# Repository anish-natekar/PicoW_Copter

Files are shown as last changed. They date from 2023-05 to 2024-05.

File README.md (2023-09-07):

# PicoW_Copter

My Pico W Copter (ignore the rubber band)

Affordable micro sub 100g coreless motor quadcopter made using Raspberry Pi pico W and controlled via an APP through WiFi.

OSHW lab - https://oshwlab.com/anishsan/picocopter
(the connectors might be different Please check the connectors for the battery separately)

First test flight (IT WORKS!!!) - https://www.youtube.com/shorts/tu2c7LCsRs8

Documentation link (Still working on this) - https://picow-copter-docs.readthedocs.io/en/latest/

APP to control PicoW Copter - [UDP Joystick](https://udpjoystick.en.aptoide.com/app) 
. delete Aptoid APP after installtion and just keep UDP Joystick APP 

Settings for the Android APP UDP joystick

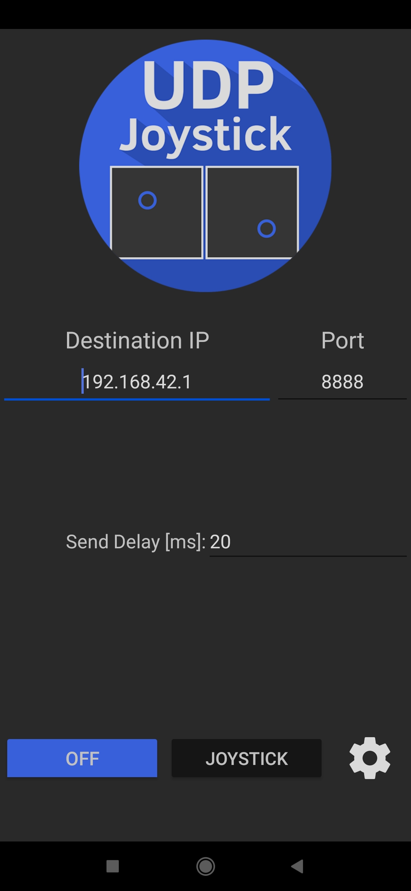
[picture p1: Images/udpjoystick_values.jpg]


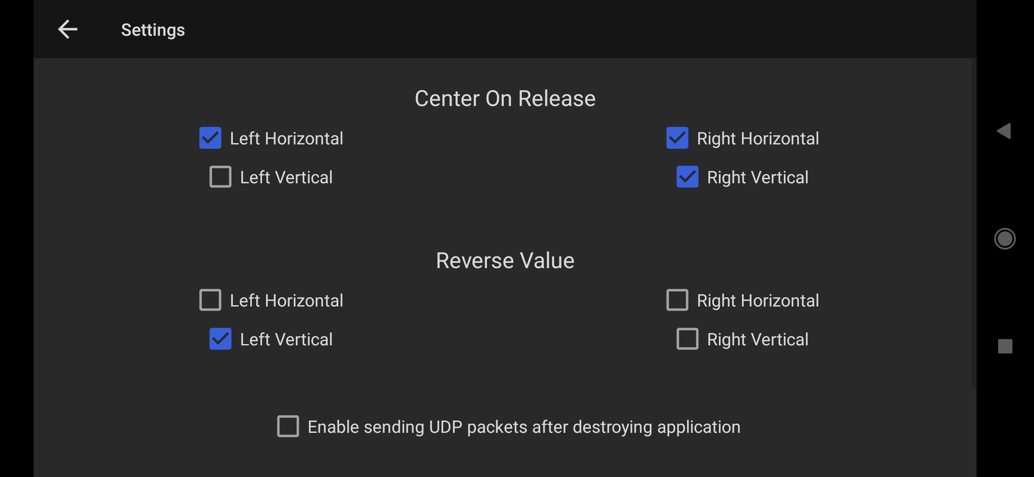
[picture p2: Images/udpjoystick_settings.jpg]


Mr. Paul Brace has designed a physical Jostick Remote Controller as an alternative to using the UDP Joystick APP. There are some benefits of a physical Joystick remote such as getting force feedback on your fingers when flying the quadcopter. You can find the details for his build here - [Hackster.io Physical Joystick Controller by Paul](https://www.hackster.io/paulsb/drone-joystick-controller-25e036)

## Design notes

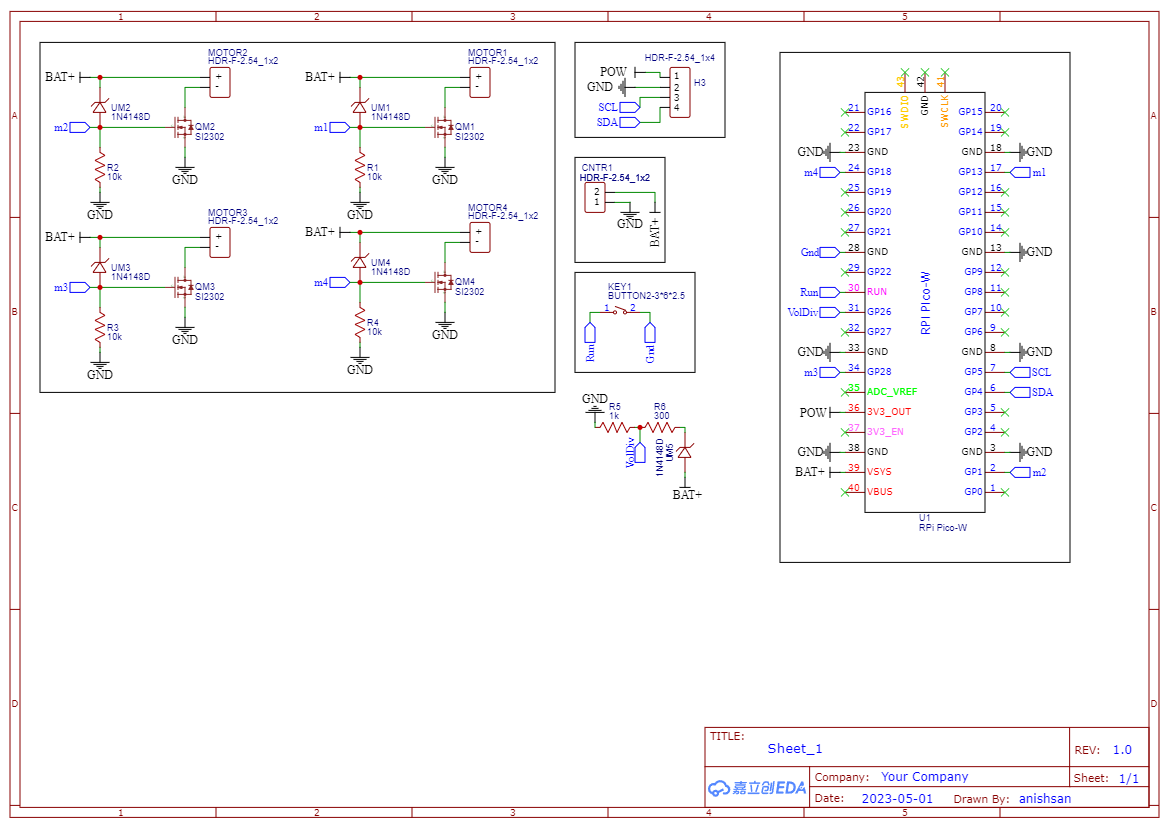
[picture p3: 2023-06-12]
Images/Schematic_PicoW_Copter.png

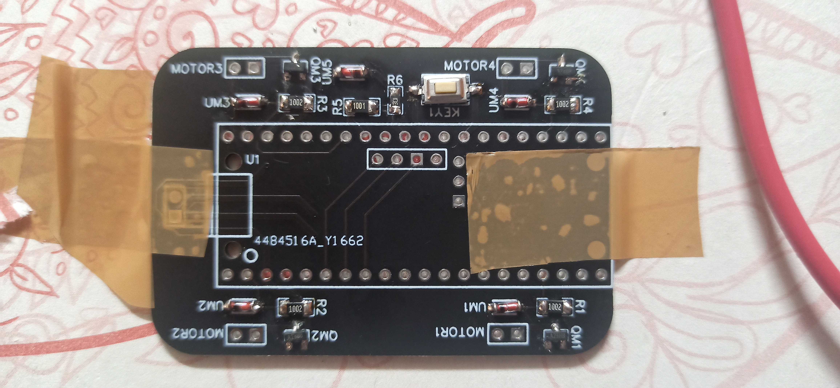
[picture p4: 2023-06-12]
Images/PCB_SMD_Top.jpg

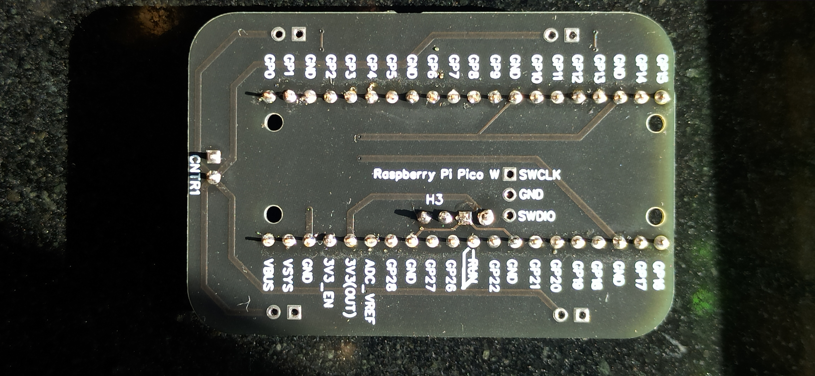
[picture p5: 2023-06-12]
Images/PCB_Bottom.jpg

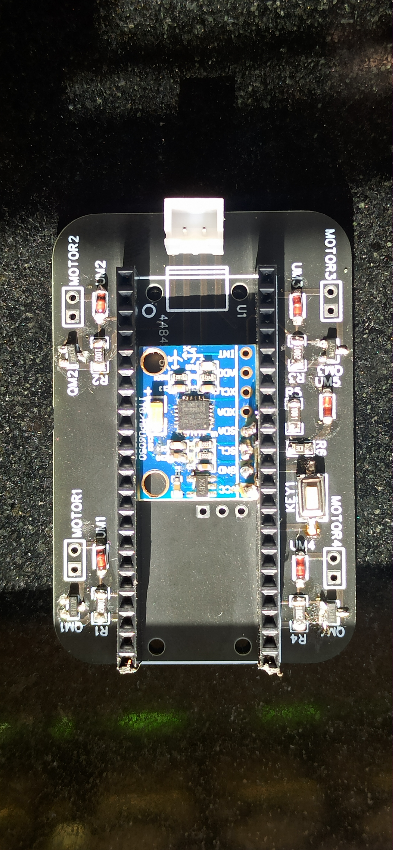
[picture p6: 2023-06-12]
Images/PCB_Top_MPU.jpg

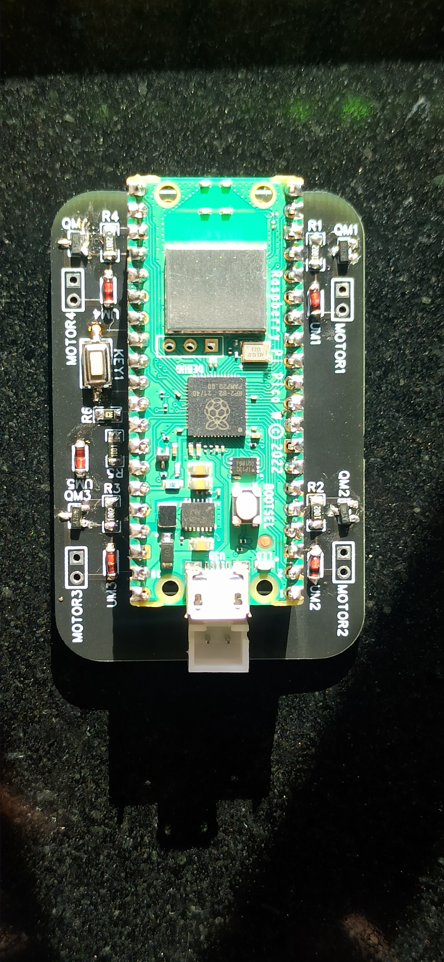
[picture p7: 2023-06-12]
Images/PCB_Top_pico.jpg

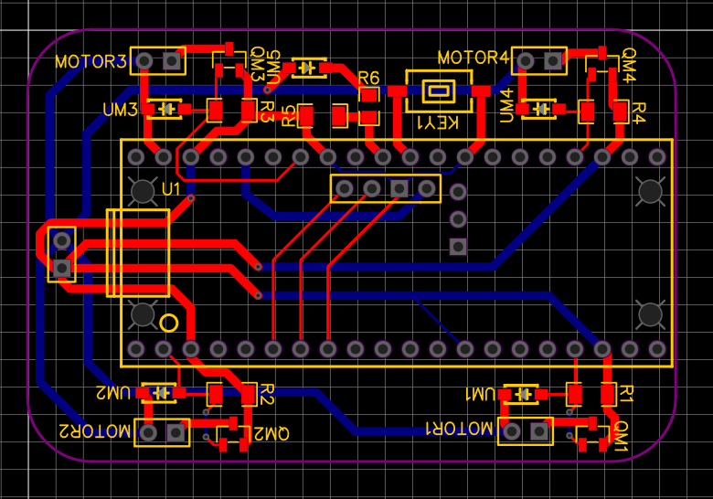
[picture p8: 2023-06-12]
Images/PCB.png

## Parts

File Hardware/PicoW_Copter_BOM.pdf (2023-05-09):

Name | Quantity | Cost | Source | Net Cost | Note
Raspberry Pi Pico W | 1 | 649 https://robu.in/product/raspberry-pi-pico-w/ | 649
Si2302 N channel Mosfet | 4 | 2.4 https://www.ktron.in/product/si2302-mosfet-sot23/ 9.6
IN4148 Diode | 4 | 2.3 https://robu.in/product/1n4148-surface-mount-zener-diode-pack-of-30/ 9.2
Male Header pins | 40 | 5.99 https://www.ktron.in/product/header-pins-40x1-2-54mm-pitch-brass/ 5.99
Female Header pins | 40 | 7.75 https://www.ktron.in/product/berg-strip-female-2-54mm-brass/ 7.75
XH male connector | 1 | 0.71 https://www.ktron.in/product/2pin-jst-xh-male-connector/ 0.71
Push button | 1 | 2.4 https://www.ktron.in/product/3x6x2-5mm-tactile-switch-smd/ 2.4
3D printed frame | 1 | 150 Robu services | 150
720 coreless motor + propellers | 4 | 445 https://robu.in/product/8520-magnetic-micro-coreless-motor-for-micro-quadcopters-2xcw-2xccw/ 445
8520 coreless motor without props | 4 | 628 | https://robu.in/product/720-magnetic-micro-coreless-motor-55-mm-propeller-for-micro-quadcopters/ 628 | This is a substitute for 720 motors
Lipo 1s 360mAh battery | 1 | 259 https://robu.in/product/orange-360-mah-1s-30c-60c-lithium-polymer-battery-pack-lipo/ 259
PCB | 1 | 150 Robu services | 160
MPU 6050 IMU | 1 | 115 https://robu.in/product/mpu-6050-gyro-sensor-2-accelerometer/ 115
BMP 280 | 1 | 35 https://robu.in/product/bmp280-barometric-pressure-and-altitude-sensor-i2c-spi-module/ 35
1S Lipo charger | 1 | 159 https://robu.in/product/4-port-dc5v-1s-rc-lithium-lipo-battery-compact-balance-charger-rc-quadcopter/ 159
TOTAL | | | | 2190.65

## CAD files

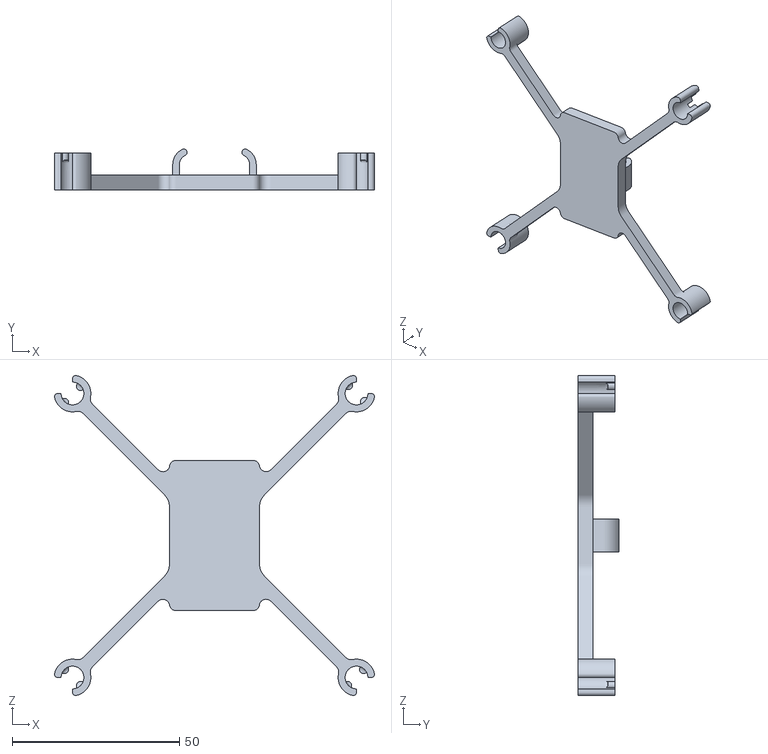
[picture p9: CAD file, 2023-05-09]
Hardware/3D_Printed_Frame/720_motor_size_files/WIZDRONE_FRAME_720.stl
95.8 x 12.2 x 95.8

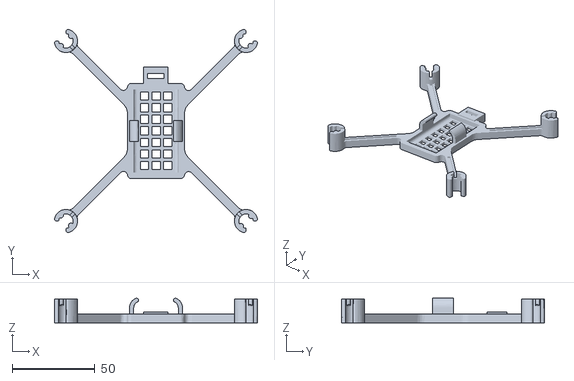
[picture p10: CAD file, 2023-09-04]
Hardware/3D_Printed_Frame/8520_motor_Paul_Brace_frame/Drone resized to fit 8.5 dia motors lighter with switch.stl
122.7 x 122.8 x 14.9

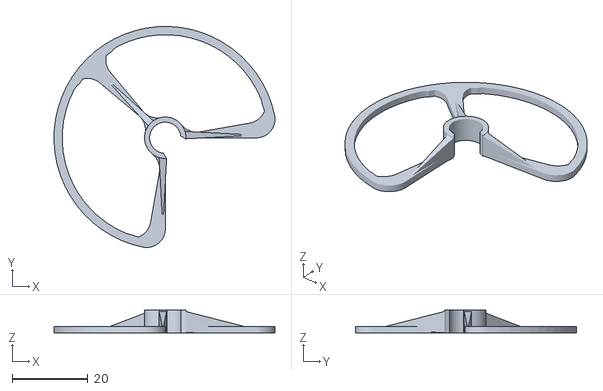
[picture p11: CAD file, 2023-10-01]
Hardware/3D_Printed_Frame/8520_motor_size_files/Prop_Guard_8520_Remix.stl
58.5 x 58.5 x 6.00

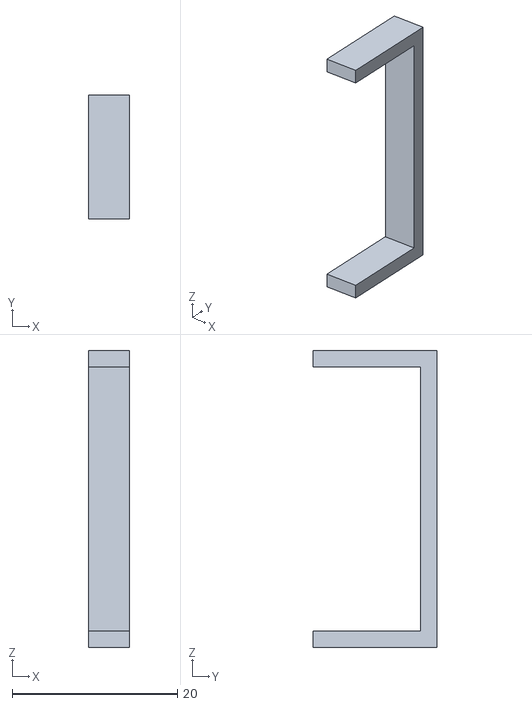
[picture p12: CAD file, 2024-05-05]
Hardware/3D_Printed_Frame/8520_motor_with_baterry_holder_Ameya_Bhagwat/drone_battery_holder.STL
5.00 x 15.0 x 36.0

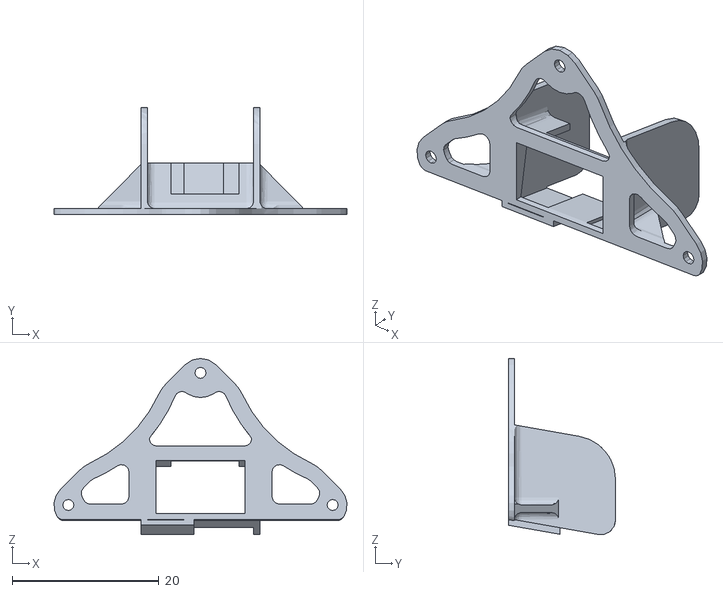
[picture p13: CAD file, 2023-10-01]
Hardware/3D_Printed_Frame/additional_files_optional/FPV 25mW AIO camera holder.STL
39.9 x 14.6 x 24.0

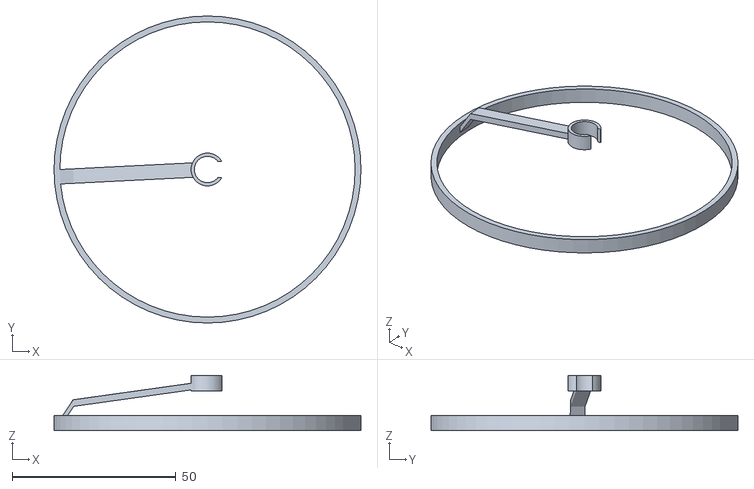
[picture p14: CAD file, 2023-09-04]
Hardware/3D_Printed_Frame/8520_motor_Paul_Brace_frame/Blade shield v4.stl
93.6 x 93.6 x 16.9

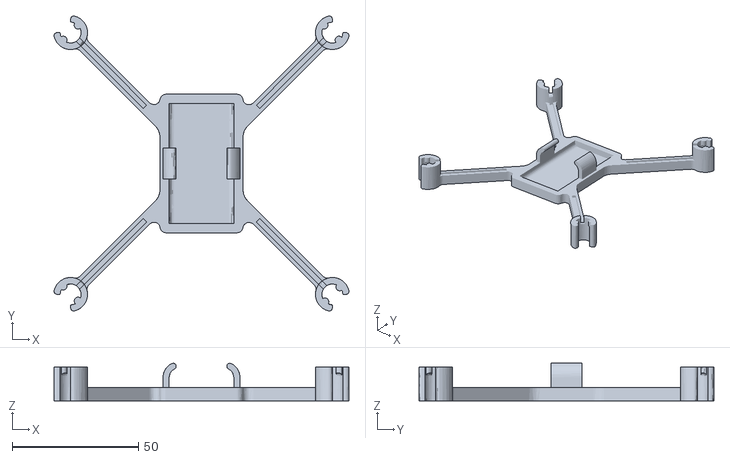
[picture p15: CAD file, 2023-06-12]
Hardware/3D_Printed_Frame/8520_motor_size_files/Scaled_Up_WizDrone_Frame_8520.stl
116.9 x 116.9 x 14.9

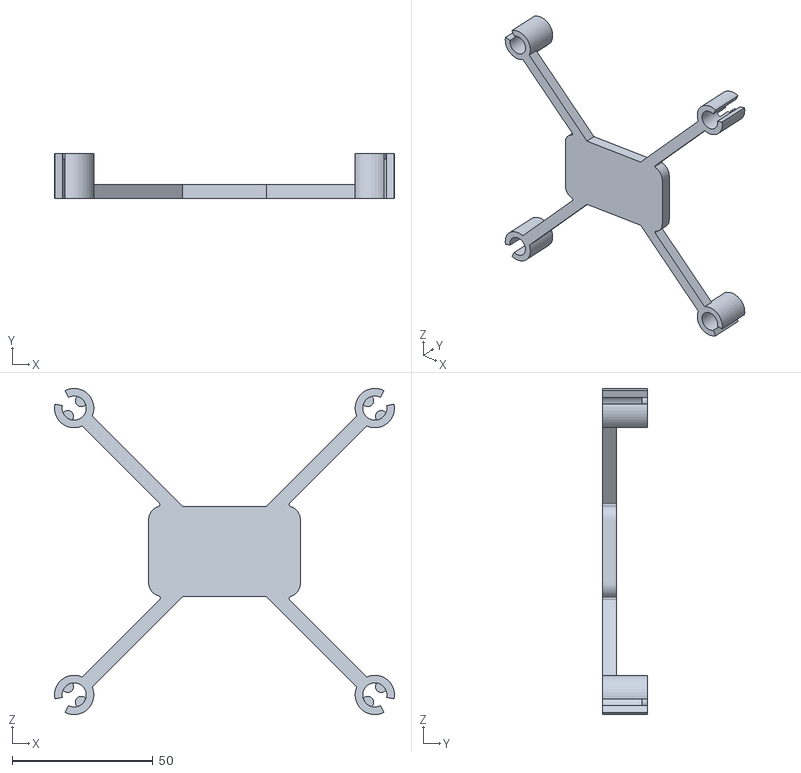
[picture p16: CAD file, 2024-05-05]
Hardware/3D_Printed_Frame/8520_motor_with_baterry_holder_Ameya_Bhagwat/8520_motor_Ameya_Bhagwat_frame.STL
120.9 x 16.0 x 116.0

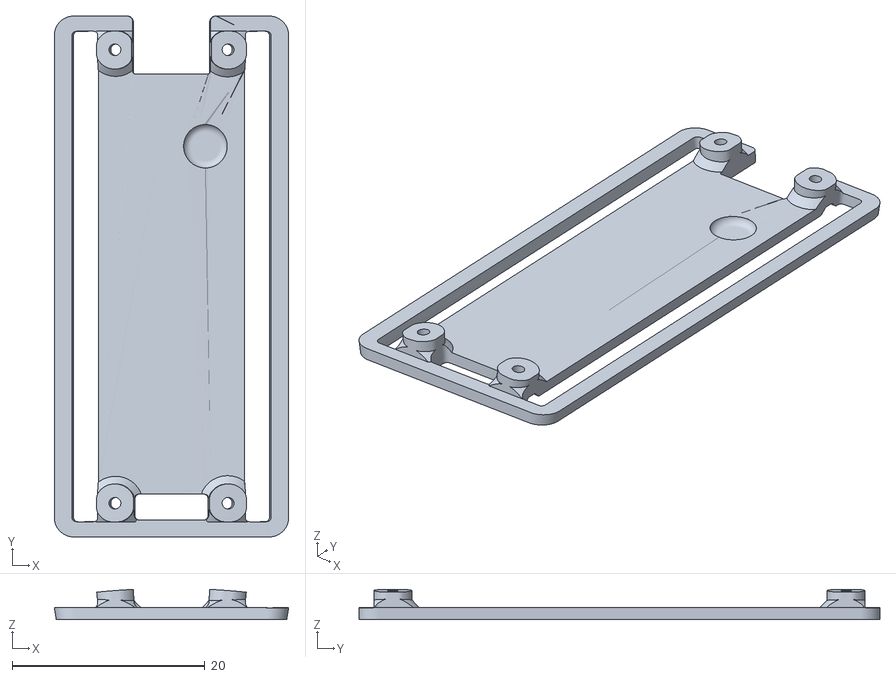
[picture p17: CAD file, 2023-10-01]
Hardware/3D_Printed_Frame/additional_files_optional/Pi_pico_top_plate.stl
24.3 x 54.0 x 3.14

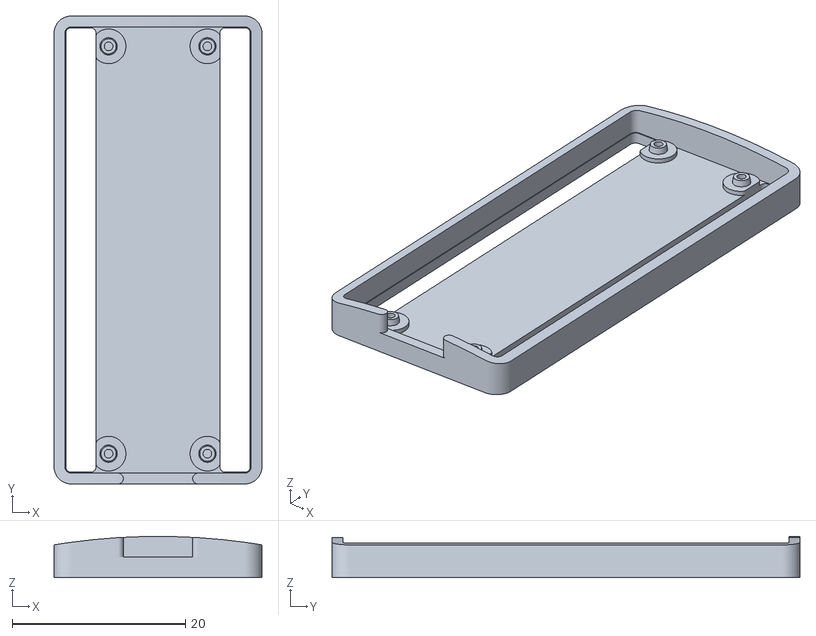
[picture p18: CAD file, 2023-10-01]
Hardware/3D_Printed_Frame/additional_files_optional/Pi_pico_bottom_plate.stl
24.0 x 54.0 x 4.74

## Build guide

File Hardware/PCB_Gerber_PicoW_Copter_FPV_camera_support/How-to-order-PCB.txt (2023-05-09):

How to Order PCB

Please refer to:
https://docs.easyeda.com/en/PCB/Order-PCB

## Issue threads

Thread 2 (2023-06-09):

Code compiled but no ap hotspot created

Shally1986, 2023-06-09:
I successfully compiled the code on a pico w . I wired only the accelerometer . I do not get any error on the serial but no hotspot is created .  Do i need to wire everything to be able get the hotspot ?

Shally1986, 2023-06-09:
I solved it

Closed 2023-06-09.

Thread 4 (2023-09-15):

flyback diode

aashlok, 2023-09-15:
In your present circuit design, what function does zener diode serve when attached to gate of mosfet? When mosfet is turned off where does back emf from motor go? I think back emf would fry mosfet in long run. A flyback 5819 schottky diode at drain of mosfet blocking from vcc seems fine for the purpose.

anish-natekar, 2023-09-16:
Hi aashlok,
the diode i used is this one- https://robu.in/product/1n4148-surface-mount-zener-diode-pack-of-30/
I referred to this video. this is not a zener diode it is a fast switching diode even if it may look like a zener diode - https://www.youtube.com/watch?v=MHtOtM_yWLw

Closed 2023-09-17.

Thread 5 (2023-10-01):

Update PCB to support XS connector for AIO FPV camera.

anish-natekar, 2023-10-01:
The PCB for the quadcopter was not designed to support a FPV camera but the Lipo battery can potentially have enough current to power a small 25mW FPV camera. The type of connector on the FPV camera is a female XS JST connector.
The PCB should have through holes for male XS JST connector to power the camera via the Lipo battery.

anish-natekar, 2023-10-01:
Added Gerber files:
Commit - https://github.com/anish-natekar/PicoW_Copter/commit/70317b23cbcddf87ffa164a068c702e18820f5d7

Closed 2023-10-01.

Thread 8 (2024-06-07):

Takeoff not stable

karimbernardet83, 2024-06-07:
Hi

Thank you very much for the tutorial !!!
I made the drone for my children (see photos).
I can't get it to take off in a stable manner. It always goes to one side just by increasing the throttle (I use my phone and udp joystick) and it always ends up turning around. I checked that the propellers are ok and in the right place.
If you have any idea what I could check.
Thank you so much
Karim

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

karimbernardet83, 2024-06-14:
With a video :-)

https://drive.google.com/file/d/13v4oZYKWqUHTXwSxi67sw0vTN-VnNnNx/view?usp=drive_link

karimbernardet83, 2024-09-11:
Got it working

anish-natekar, 2024-11-12:
Congrats. Sorry I didn't reply back when you needed help. I am not able to manage time these days for building things hope to get back soon and be more active on github.

Closed 2024-09-11.

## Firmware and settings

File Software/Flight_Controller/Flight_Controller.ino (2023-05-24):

#include <Wire.h>                          //Include the Wire.h library so we can communicate with the gyro.
#include <WiFi.h>
#include <WiFiUdp.h>

#define I2C_CLK_FREQ 400000 // 400kHz
const u_int8_t IMUAddress = 0x68;  // Address for MPU6050 IMU sensor

#ifndef APSSID
#define APSSID "PicoW"
#define APPSW "password"
#endif
#define UDP_PKT_MAX_SIZE 16

unsigned int localPort = 8888;
char packetBuffer[UDP_PKT_MAX_SIZE + 1];

WiFiUDP Udp;  // Object for WiFi UDP class

#define MOT_TOP_LEFT 18
#define MOT_TOP_RIGHT 13
#define MOT_BOTTOM_LEFT 28
#define MOT_BOTTOM_RIGHT 1
#define sensitivity 2

///////////////////////////////////////////////////////////////////////////////////////////////////////////////////////////////////////
//PID gain and limit settings
///////////////////////////////////////////////////////////////////////////////////////////////////////////////////////////////////////
float pid_p_gain_roll = 1.3;               //Gain setting for the roll P-controller was 2.05
float pid_i_gain_roll = 0.013;              //Gain setting for the roll I-controller 0.04
float pid_d_gain_roll = 14.0;              //Gain setting for the roll D-controller was 11.0
int pid_max_roll = 300;                    //Maximum output of the PID-controller (+/-)

float pid_p_gain_pitch = pid_p_gain_roll;  //Gain setting for the pitch P-controller.
float pid_i_gain_pitch = pid_i_gain_roll;  //Gain setting for the pitch I-controller.
float pid_d_gain_pitch = pid_d_gain_roll;  //Gain setting for the pitch D-controller.
int pid_max_pitch = pid_max_roll;          //Maximum output of the PID-controller (+/-)

float pid_p_gain_yaw = 8.5;                //Gain setting for the pitch P-controller. //4.0
float pid_i_gain_yaw = 0.005;               //Gain setting for the pitch I-controller. //0.02
float pid_d_gain_yaw = 0.0;                //Gain setting for the pitch D-controller.
int pid_max_yaw = 300;                     //Maximum output of the PID-controller (+/-)

boolean auto_level = true;                 //Auto level on (true) or off (false)

///////////////////////////////////////////////////////////////////////////////////////////////////////////////////////////////////////
//Declaring global variables
///////////////////////////////////////////////////////////////////////////////////////////////////////////////////////////////////////
byte last_channel_1, last_channel_2, last_channel_3, last_channel_4;
byte highByte, lowByte;
volatile int receiver_input_channel_1 = 0, receiver_input_channel_2 = 0, receiver_input_channel_3 = 0, receiver_input_channel_4 = 0;
int counter_channel_1, counter_channel_2, counter_channel_3, counter_channel_4, loop_counter;
int esc_1, esc_2, esc_3, esc_4;
int throttle, battery_voltage;
int cal_int, start, gyro_address;
int receiver_input[5];
int temperature;
int16_t acc_axis[4], gyro_axis[4];
float roll_level_adjust, pitch_level_adjust;

long acc_x, acc_y, acc_z, acc_total_vector;
unsigned long timer_channel_1, timer_channel_2, timer_channel_3, timer_channel_4, esc_timer, esc_loop_timer;
unsigned long timer_1, timer_2, timer_3, timer_4, current_time;
unsigned long loop_timer;
double gyro_pitch, gyro_roll, gyro_yaw;
double gyro_axis_cal[4];
float pid_error_temp;
float pid_i_mem_roll, pid_roll_setpoint, gyro_roll_input, pid_output_roll, pid_last_roll_d_error;
float pid_i_mem_pitch, pid_pitch_setpoint, gyro_pitch_input, pid_output_pitch, pid_last_pitch_d_error;
float pid_i_mem_yaw, pid_yaw_setpoint, gyro_yaw_input, pid_output_yaw, pid_last_yaw_d_error;
float angle_roll_acc, angle_pitch_acc, angle_pitch, angle_roll;
boolean gyro_angles_set;

///////////////////////////////////////////////////////////////////////////////////////////////////////////////////////////////////////
//Setup routine
///////////////////////////////////////////////////////////////////////////////////////////////////////////////////////////////////////
void setup(){
  
  analogWriteFreq(500); // PWM frequency 500 Hz
  analogWriteRange(1000); // value coresponding to 100% PWM duty cycle

  Serial.begin(115200);
  gyro_address = IMUAddress;      
  Wire.setClock(I2C_CLK_FREQ);   
  Wire.begin();                                                             //Start the I2C as master.

  pinMode(MOT_TOP_LEFT, OUTPUT);
  pinMode(MOT_TOP_RIGHT, OUTPUT);
  pinMode(MOT_BOTTOM_LEFT, OUTPUT);
  pinMode(MOT_BOTTOM_RIGHT, OUTPUT);
  pinMode(LED_BUILTIN, OUTPUT);
  analogWrite(MOT_TOP_LEFT, 0);
  analogWrite(MOT_TOP_RIGHT, 0);
  analogWrite(MOT_BOTTOM_LEFT, 0);
  analogWrite(MOT_BOTTOM_RIGHT, 0);
  
  //Use the led on the Arduino for startup indication.
  digitalWrite(LED_BUILTIN,HIGH);                                                    //Turn on the warning led.

  set_gyro_registers();                                                     //Set the specific gyro registers.

  //Let's take multiple gyro data samples so we can determine the average gyro offset (calibration).
  for (cal_int = 0; cal_int < 2000 ; cal_int ++){                           //Take 2000 readings for calibration.
    if(cal_int % 15 == 0)
      digitalWrite(LED_BUILTIN, !digitalRead(LED_BUILTIN));                //Change the led status to indicate calibration.
    gyro_signalen();                                                        //Read the gyro output.
    gyro_axis_cal[1] += gyro_axis[1];   
    gyro_axis_cal[2] += gyro_axis[2];
    gyro_axis_cal[3] += gyro_axis[3];
    delay(4);                                                               //Wait 3 milliseconds before the next loop.
  }
  //Now that we have 2000 measures, we need to devide by 2000 to get the average gyro offset.
  gyro_axis_cal[1] /= 2000;                                                 //Divide the roll total by 2000.
  gyro_axis_cal[2] /= 2000;                                                 //Divide the pitch total by 2000.
  gyro_axis_cal[3] /= 2000;                                                 //Divide the yaw total by 2000.                                                //Set PCINT3 (digital input 11)to trigger an interrupt on state change.

  WiFi.mode(WIFI_AP);
  WiFi.begin(APSSID, APPSW);
  while(WiFi.status() != WL_CONNECTED) {
    Serial.print('.');    
    delay(500);    
  }
  Udp.begin(localPort);  
  //Wait until the receiver is active and the throtle is set to the lower position.
  while(receiver_input_channel_3 < 990 || receiver_input_channel_3 > 1020 || receiver_input_channel_4 < 1400){
    int packetSize = Udp.parsePacket();
    if(packetSize) {
      int n = Udp.read(packetBuffer, UDP_PKT_MAX_SIZE);
      packetBuffer[n] = '\0';
      char ch1[5], ch2[5], ch3[5], ch4[5];
      ch1[4] = '\0'; ch2[4] = '\0'; ch3[4] = '\0'; ch4[4] = '\0';
      for(int i=0; i<4; i++) {
        ch4[i] = packetBuffer[i];
        ch3[i] = packetBuffer[i+4];
        ch1[i] = packetBuffer[i+8];
        ch2[i] = packetBuffer[i+12];     
      }
      receiver_input_channel_1 = atoi(ch1); // ROLL
      receiver_input_channel_2 = atoi(ch2); // PITCH
      receiver_input_channel_3 = atoi(ch3); // THROTTLE
      receiver_input_channel_4 = atoi(ch4); // YAW
    }
    start ++;
    delay(3);                                                               //Wait 3 milliseconds before the next loop.
    if(start == 125){                                                       //Every 125 loops (500ms).
      digitalWrite(LED_BUILTIN, !digitalRead(LED_BUILTIN));                                   //Change the led status.
      start = 0;                                                            //Start again at 0.
    }
  }
  start = 0;                                                                //Set start back to 0.

  //Load the battery voltage to the battery_voltage variable.
  //65 is the voltage compensation for the diode.
  //12.6V equals ~5V @ Analog 0.
  //12.6V equals 1023 analogRead(0).
  //1260 / 1023 = 1.2317.
  //The variable battery_voltage holds 1050 if the battery voltage is 10.5V.
  //battery_voltage = (analogRead(0) + 65) * 1.2317;

  loop_timer = micros();                                                    //Set the timer for the next loop.

  //When everything is done, turn off the led.
  digitalWrite(LED_BUILTIN,LOW);                                                     //Turn off the warning led.
}
///////////////////////////////////////////////////////////////////////////////////////////////////////////////////////////////////////
//Main program loop
///////////////////////////////////////////////////////////////////////////////////////////////////////////////////////////////////////
void loop(){
  int packetSize = Udp.parsePacket();
  if(packetSize) {
      int n = Udp.read(packetBuffer, UDP_PKT_MAX_SIZE);
      packetBuffer[n] = '\0';
      char ch1[5], ch2[5], ch3[5], ch4[5];
      ch1[4] = '\0'; ch2[4] = '\0'; ch3[4] = '\0'; ch4[4] = '\0';
      for(int i=0; i<4; i++) {
        ch4[i] = packetBuffer[i];
        ch3[i] = packetBuffer[i+4];
        ch1[i] = packetBuffer[i+8];
        ch2[i] = packetBuffer[i+12];     
      }
      receiver_input_channel_1 = atoi(ch1); // ROLL
      receiver_input_channel_2 = atoi(ch2); // PITCH
      receiver_input_channel_3 = atoi(ch3); // THROTTLE
      receiver_input_channel_4 = atoi(ch4); // YAW
    }

  //65.5 = 1 deg/sec (check the datasheet of the MPU-6050 for more information).
  gyro_roll_input = (gyro_roll_input * 0.7) + ((gyro_roll / 65.5) * 0.3);   //Gyro pid input is deg/sec.
  gyro_pitch_input = (gyro_pitch_input * 0.7) + ((gyro_pitch / 65.5) * 0.3);//Gyro pid input is deg/sec.
  gyro_yaw_input = (gyro_yaw_input * 0.7) + ((gyro_yaw / 65.5) * 0.3);      //Gyro pid input is deg/sec.

//  Serial.print(gyro_roll_input);
//  Serial.print(", ");
//  Serial.print(gyro_pitch_input);
//  Serial.print(", ");
//  Serial.print(gyro_yaw_input);
//  Serial.println();
//  

  ////////////////////////////////////////////////////////////////////////////////////////////////////
  //This is the added IMU code from the videos:
  //https://youtu.be/4BoIE8YQwM8
  //https://youtu.be/j-kE0AMEWy4
  ////////////////////////////////////////////////////////////////////////////////////////////////////
  
  //Gyro angle calculations
  //0.0000611 = 1 / (250Hz / 65.5)
  angle_pitch += gyro_pitch * 0.0000611;                                    //Calculate the traveled pitch angle and add this to the angle_pitch variable.
  angle_roll += gyro_roll * 0.0000611;                                      //Calculate the traveled roll angle and add this to the angle_roll variable.

  //0.000001066 = 0.0000611 * (3.142(PI) / 180degr) The Arduino sin function is in radians
  angle_pitch -= angle_roll * sin(gyro_yaw * 0.000001066);                  //If the IMU has yawed transfer the roll angle to the pitch angel.
  angle_roll += angle_pitch * sin(gyro_yaw * 0.000001066);                  //If the IMU has yawed transfer the pitch angle to the roll angel.

  //Accelerometer angle calculations
  acc_total_vector = sqrt((acc_x*acc_x)+(acc_y*acc_y)+(acc_z*acc_z));       //Calculate the total accelerometer vector.
  
  if(abs(acc_y) < acc_total_vector){                                        //Prevent the asin function to produce a NaN
    angle_pitch_acc = asin((float)acc_y/acc_total_vector)* 57.296;          //Calculate the pitch angle.
  }
  if(abs(acc_x) < acc_total_vector){                                        //Prevent the asin function to produce a NaN
    angle_roll_acc = asin((float)acc_x/acc_total_vector)* -57.296;          //Calculate the roll angle.
  }
  
  //Place the MPU-6050 spirit level and note the values in the following two lines for calibration.
  angle_pitch_acc -= 0.0;                                                   //Accelerometer calibration value for pitch.
  angle_roll_acc -= 0.0;                                                    //Accelerometer calibration value for roll.
  
  angle_pitch = angle_pitch * 0.9996 + angle_pitch_acc * 0.0004;            //Correct the drift of the gyro pitch angle with the accelerometer pitch angle.
  angle_roll = angle_roll * 0.9996 + angle_roll_acc * 0.0004;               //Correct the drift of the gyro roll angle with the accelerometer roll angle.

  pitch_level_adjust = angle_pitch * 15;                                    //Calculate the pitch angle correction
  roll_level_adjust = angle_roll * 15;                                      //Calculate the roll angle correction

  if(!auto_level){                                                          //If the quadcopter is not in auto-level mode
    pitch_level_adjust = 0;                                                 //Set the pitch angle correction to zero.
    roll_level_adjust = 0;                                                  //Set the roll angle correcion to zero.
  }


  //For starting the motors: throttle low and yaw left (step 1).
  if(receiver_input_channel_3 < 1050 && receiver_input_channel_4 < 1050)start = 1;
  //When yaw stick is back in the center position start the motors (step 2).
  if(start == 1 && receiver_input_channel_3 < 1050 && receiver_input_channel_4 > 1450){
    start = 2;

    angle_pitch = angle_pitch_acc;                                          //Set the gyro pitch angle equal to the accelerometer pitch angle when the quadcopter is started.
    angle_roll = angle_roll_acc;                                            //Set the gyro roll angle equal to the accelerometer roll angle when the quadcopter is started.
    gyro_angles_set = true;                                                 //Set the IMU started flag.

    //Reset the PID controllers for a bumpless start.
    pid_i_mem_roll = 0;
    pid_last_roll_d_error = 0;
    pid_i_mem_pitch = 0;
    pid_last_pitch_d_error = 0;
    pid_i_mem_yaw = 0;
    pid_last_yaw_d_error = 0;
  }
  //Stopping the motors: throttle low and yaw right.
  if(start == 2 && receiver_input_channel_3 < 1050 && receiver_input_channel_4 > 1950)start = 0;

  //The PID set point in degrees per second is determined by the roll receiver input.
  //In the case of deviding by 3 the max roll rate is aprox 164 degrees per second ( (500-8)/3 = 164d/s ).
  pid_roll_setpoint = 0;
  //We need a little dead band of 16us for better results.
  if(receiver_input_channel_1 > 1508)pid_roll_setpoint = receiver_input_channel_1 - 1508;
  else if(receiver_input_channel_1 < 1492)pid_roll_setpoint = receiver_input_channel_1 - 1492;

  pid_roll_setpoint -= roll_level_adjust;                                   //Subtract the angle correction from the standardized receiver roll input value.
  pid_roll_setpoint /= 3.0;                                                 //Divide the setpoint for the PID roll controller by 3 to get angles in degrees.


  //The PID set point in degrees per second is determined by the pitch receiver input.
  //In the case of deviding by 3 the max pitch rate is aprox 164 degrees per second ( (500-8)/3 = 164d/s ).
  pid_pitch_setpoint = 0;
  //We need a little dead band of 16us for better results.
  if(receiver_input_channel_2 > 1508)pid_pitch_setpoint = receiver_input_channel_2 - 1508;
  else if(receiver_input_channel_2 < 1492)pid_pitch_setpoint = receiver_input_channel_2 - 1492;

  pid_pitch_setpoint -= pitch_level_adjust;                                  //Subtract the angle correction from the standardized receiver pitch input value.
  pid_pitch_setpoint /= 3.0;                                                 //Divide the setpoint for the PID pitch controller by 3 to get angles in degrees.

  //The PID set point in degrees per second is determined by the yaw receiver input.
  //In the case of deviding by 3 the max yaw rate is aprox 164 degrees per second ( (500-8)/3 = 164d/s ).
  pid_yaw_setpoint = 0;
  //We need a little dead band of 16us for better results.
  if(receiver_input_channel_3 > 1050){ //Do not yaw when turning off the motors.
    if(receiver_input_channel_4 > 1508)pid_yaw_setpoint = (receiver_input_channel_4 - 1508)/3.0;
    else if(receiver_input_channel_4 < 1492)pid_yaw_setpoint = (receiver_input_channel_4 - 1492)/3.0;
  }
  
  calculate_pid();                                                            //PID inputs are known. So we can calculate the pid output.

  //The battery voltage is needed for compensation.
  //A complementary filter is used to reduce noise.
  //0.09853 = 0.08 * 1.2317.
  //battery_voltage = battery_voltage * 0.92 + (analogRead(0) + 65) * 0.09853;

  //Turn on the led if battery voltage is to low.
  //if(battery_voltage < 1000 && battery_voltage > 600)digitalWrite(12, HIGH);


  throttle = receiver_input_channel_3;                                      //We need the throttle signal as a base signal.

  if (start == 2){                                                          //The motors are started.
    if (throttle > 1800) throttle = 1800;                                   //We need some room to keep full control at full throttle.
    esc_1 = throttle - pid_output_pitch + pid_output_roll - pid_output_yaw; //Calculate the pulse for esc 1 (front-right - CCW)
    esc_2 = throttle + pid_output_pitch + pid_output_roll + pid_output_yaw; //Calculate the pulse for esc 2 (rear-right - CW)
    esc_3 = throttle + pid_output_pitch - pid_output_roll - pid_output_yaw; //Calculate the pulse for esc 3 (rear-left - CCW)
    esc_4 = throttle - pid_output_pitch - pid_output_roll + pid_output_yaw; //Calculate the pulse for esc 4 (front-left - CW)

    // if (battery_voltage < 1240 && battery_voltage > 800){                   //Is the battery connected?
    //   esc_1 += esc_1 * ((1240 - battery_voltage)/(float)3500);              //Compensate the esc-1 pulse for voltage drop.
    //   esc_2 += esc_2 * ((1240 - battery_voltage)/(float)3500);              //Compensate the esc-2 pulse for voltage drop.
    //   esc_3 += esc_3 * ((1240 - battery_voltage)/(float)3500);              //Compensate the esc-3 pulse for voltage drop.
    //   esc_4 += esc_4 * ((1240 - battery_voltage)/(float)3500);              //Compensate the esc-4 pulse for voltage drop.
    // } 

    if (esc_1 < 1100) esc_1 = 1100;                                         //Keep the motors running.
    if (esc_2 < 1100) esc_2 = 1100;                                         //Keep the motors running.
    if (esc_3 < 1100) esc_3 = 1100;                                         //Keep the motors running.
    if (esc_4 < 1100) esc_4 = 1100;                                         //Keep the motors running.

    if(esc_1 > 2000)esc_1 = 2000;                                           //Limit the esc-1 pulse to 2000us.
    if(esc_2 > 2000)esc_2 = 2000;                                           //Limit the esc-2 pulse to 2000us.
    if(esc_3 > 2000)esc_3 = 2000;                                           //Limit the esc-3 pulse to 2000us.
    if(esc_4 > 2000)esc_4 = 2000;                                           //Limit the esc-4 pulse to 2000us.  
  }

  else{
    esc_1 = 1000;                                                           //If start is not 2 keep a 1000us pulse for ess-1.
    esc_2 = 1000;                                                           //If start is not 2 keep a 1000us pulse for ess-2.
    esc_3 = 1000;                                                           //If start is not 2 keep a 1000us pulse for ess-3.
    esc_4 = 1000;                                                           //If start is not 2 keep a 1000us pulse for ess-4.
  }

  ////////////////////////////////////////////////////////////////////////////////////////////////////
  //Creating the pulses for the ESC's is explained in this video:
  //https://youtu.be/fqEkVcqxtU8
  ////////////////////////////////////////////////////////////////////////////////////////////////////

  //! ! ! ! ! ! ! ! ! ! ! ! ! ! ! ! ! ! ! ! ! ! ! ! ! ! ! ! ! ! ! ! ! ! ! ! ! ! ! ! ! ! ! ! ! ! ! ! ! !
  //Because of the angle calculation the loop time is getting very important. If the loop time is 
  //longer or shorter than 4000us the angle calculation is off. If you modify the code make sure 
  //that the loop time is still 4000us and no longer! More information can be found on 
  //the Q&A page: 
  //! ! ! ! ! ! ! ! ! ! ! ! ! ! ! ! ! ! ! ! ! ! ! ! ! ! ! ! ! ! ! ! ! ! ! ! ! ! ! ! ! ! ! ! ! ! ! ! ! !
    
  if(micros() - loop_timer > 4050)digitalWrite(LED_BUILTIN, HIGH);                   //Turn on the LED if the loop time exceeds 4050us.
  
  //All the information for controlling the motor's is available.
  //The refresh rate is 250Hz. That means the esc's need there pulse every 4ms.
  while(micros() - loop_timer < 4000);                                      //We wait until 4000us are passed.
  loop_timer = micros();                                                    //Set the timer for the next loop.

  esc_1 = map(esc_1, 1000, 2000, 0, 1000);
  esc_2 = map(esc_2, 1000, 2000, 0, 1000);
  esc_3 = map(esc_3, 1000, 2000, 0, 1000);
  esc_4 = map(esc_4, 1000, 2000, 0, 1000);

  analogWrite(MOT_TOP_RIGHT, esc_1);
  analogWrite(MOT_BOTTOM_RIGHT, esc_2);
  analogWrite(MOT_BOTTOM_LEFT, esc_3);
  analogWrite(MOT_TOP_LEFT, esc_4);
  //There is always 1000us of spare time. So let's do something usefull that is very time consuming.
  //Get the current gyro and receiver data and scale it to degrees per second for the pid calculations.
  gyro_signalen();
}
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

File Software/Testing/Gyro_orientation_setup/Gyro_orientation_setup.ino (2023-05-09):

#include <Wire.h>

#define I2C_CLK_FREQ 400000

int cal_int;
float gyro_roll_cal, gyro_pitch_cal, gyro_yaw_cal;
float gyro_roll, gyro_yaw, gyro_pitch;
byte roll_axis, pitch_axis, yaw_axis;
byte lowByte, highByte, type, gyro_address, error = 0, clockspeed_ok;
byte gyro_check_byte;
unsigned long timer;

void start_gyro() {
  Wire.beginTransmission(gyro_address);                             //Start communication with the gyro
    Wire.write(0x6B);                                            //PWR_MGMT_1 register
    Wire.write(0x00);                                            //Set to zero to turn on the gyro
    Wire.endTransmission();                                      //End the transmission
    
    Wire.beginTransmission(gyro_address);                             //Start communication with the gyro
    Wire.write(0x6B);                                            //Start reading @ register 28h and auto increment with every read
    Wire.endTransmission();                                      //End the transmission
    Wire.requestFrom(gyro_address, 1);                                //Request 1 bytes from the gyro
    while(Wire.available() < 1);                                 //Wait until the 1 byte is received
    Serial.print(F("Register 0x6B is set to:"));
    Serial.println(Wire.read(),BIN);
    
    Wire.beginTransmission(gyro_address);                             //Start communication with the gyro
    Wire.write(0x1B);                                            //GYRO_CONFIG register
    Wire.write(0x08);                                            //Set the register bits as 00001000 (500dps full scale)
    Wire.endTransmission();                                      //End the transmission
    
    Wire.beginTransmission(gyro_address);                             //Start communication with the gyro (adress 1101001)
    Wire.write(0x1B);                                            //Start reading @ register 28h and auto increment with every read
    Wire.endTransmission();                                      //End the transmission
    Wire.requestFrom(gyro_address, 1);                                //Request 1 bytes from the gyro
    while(Wire.available() < 1);                                 //Wait until the 1 byte is received
    Serial.print(F("Register 0x1B is set to:"));
    Serial.println(Wire.read(),BIN);
}

void gyro_signalen() {
    int16_t gy_roll, gy_pitch, gy_yaw;
    Wire.beginTransmission(gyro_address);                             //Start communication with the gyro
    Wire.write(0x43);                                            //Start reading @ register 43h and auto increment with every read
    Wire.endTransmission();                                      //End the transmission
    Wire.requestFrom(gyro_address,6);                                 //Request 6 bytes from the gyro
    while(Wire.available() < 6);                                 //Wait until the 6 bytes are received
    gy_roll = Wire.read()<<8|Wire.read();
    gyro_roll = (float)gy_roll;                       //Read high and low part of the angular data
    if(cal_int == 2000)gyro_roll -= gyro_roll_cal;               //Only compensate after the calibration
    gy_pitch = Wire.read()<<8|Wire.read();
    gyro_pitch = (float)gy_pitch;                      //Read high and low part of the angular data
    if(cal_int == 2000)gyro_pitch -= gyro_pitch_cal;             //Only compensate after the calibration
    gy_yaw = Wire.read()<<8|Wire.read();                         //Read high and low part of the angular data
    gyro_yaw = (float)gy_yaw;
    if(cal_int == 2000)gyro_yaw -= gyro_yaw_cal;                 //Only compensate after the calibration  
}


//Check if the angular position of a gyro axis is changing within 10 seconds
void check_gyro_axes(byte movement){
  byte trigger_axis = 0;
  float gyro_angle_roll, gyro_angle_pitch, gyro_angle_yaw;
  //Reset all axes
  gyro_angle_roll = 0;
  gyro_angle_pitch = 0;
  gyro_angle_yaw = 0;
  gyro_signalen();
  timer = millis() + 10000;    
  while(timer > millis() && gyro_angle_roll > -30 && gyro_angle_roll < 30 && gyro_angle_pitch > -30 && gyro_angle_pitch < 30 && gyro_angle_yaw > -30 && gyro_angle_yaw < 30){
    gyro_signalen();
    gyro_angle_roll += gyro_roll * 0.0000611;          // 0.0000611 = 1 / 65.5 (LSB degr/s) / 250(Hz)
    gyro_angle_pitch += gyro_pitch * 0.0000611;
    gyro_angle_yaw += gyro_yaw * 0.0000611;
    delayMicroseconds(3700); //Loop is running @ 250Hz. +/-300us is used for communication with the gyro
  }
  //Assign the moved axis to the orresponding function (pitch, roll, yaw)
  if((gyro_angle_roll < -30 || gyro_angle_roll > 30) && gyro_angle_pitch > -30 && gyro_angle_pitch < 30 && gyro_angle_yaw > -30 && gyro_angle_yaw < 30){
    // Roll detected i.e. rotation about X axis
    gyro_check_byte |= 0b00000001;
    if(gyro_angle_roll < 0)trigger_axis = 0b10000001;
    else trigger_axis = 0b00000001;
  }
  if((gyro_angle_pitch < -30 || gyro_angle_pitch > 30) && gyro_angle_roll > -30 && gyro_angle_roll < 30 && gyro_angle_yaw > -30 && gyro_angle_yaw < 30){
    // Pitch detected i.e. rotation about Y axis
    gyro_check_byte |= 0b00000010;
    if(gyro_angle_pitch < 0)trigger_axis = 0b10000010;
    else trigger_axis = 0b00000010;
  }
  if((gyro_angle_yaw < -30 || gyro_angle_yaw > 30) && gyro_angle_roll > -30 && gyro_angle_roll < 30 && gyro_angle_pitch > -30 && gyro_angle_pitch < 30){
    // Yaw detected i.e. rotation about Z axis
    gyro_check_byte |= 0b00000100;
    if(gyro_angle_yaw < 0)trigger_axis = 0b10000011;
    else trigger_axis = 0b00000011;
  }
  
  if(trigger_axis == 0){
    error = 1;
    Serial.println(F("No angular motion is detected in the last 10 seconds!!! (ERROR 4)"));
  }
  else
  if(movement == 1)roll_axis = trigger_axis;
  if(movement == 2)pitch_axis = trigger_axis;
  if(movement == 3)yaw_axis = trigger_axis;
  
}
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

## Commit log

2023-05-09 added software and hardware
    [Drill_NPTH_Through.DRL, Drill_PTH_Through.DRL, Drill_PTH_Through_Via.DRL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]
2023-05-21 updated and tested pcb and flight controller
2023-05-24 updated PID values
2023-06-12 added images and stl file for 8520 frame
    [Scaled_Up_WizDrone_Frame_8520.stl, WIZDRONE_FRAME_720.stl]
2023-08-31 New STL filed
    Modified frame with switch holder and propeller guards.
    [Blade shield v4.stl, Drone resized to fit 8.5 dia motors lighter with switch.stl]
2023-08-31 Revert "New STL filed"
    This reverts commit bf463e78c51046e3ef4851c6ed23d3807cc84b53.
    [Blade shield v4.stl, Drone resized to fit 8.5 dia motors lighter with switch.stl]
2023-08-31 New STL Files Added
    New STL frame - lighter and a switch holder added.
    New STL propeller guard added
    [Blade shield v4.stl, Drone resized to fit 8.5 dia motors lighter with switch.stl]
2023-10-01 added and segregated STL files.
    added stl files for quadcopter frame. Segregated files according to motor size
    currently supporting 720 & 8520 sizes. Added additional optional files for FPV camera holder and pico W case.
    [Blade shield v4.stl, Drone resized to fit 8.5 dia motors lighter with switch.stl, FPV 25mW AIO camera holder.STL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]
2023-10-01 added Gerber file for FPV camera supported PCB
    This PCB has two additional ports for XS connectors these can be used to power a small 25mW FPV camera from the 1s battery.
    [Drill_NPTH_Through.DRL, Drill_PTH_Through.DRL, Drill_PTH_Through_Via.DRL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]
2024-05-05 added inside folder
    [8520_motor_Ameya_Bhagwat_frame.STL, drone_battery_holder.STL]
